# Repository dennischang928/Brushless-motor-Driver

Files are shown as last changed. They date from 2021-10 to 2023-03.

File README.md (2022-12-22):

# BLDC Driver

## Electronics

- MCU
  - STM32F103C8T6 (Blue pill)
    - Serial PIN
      - RX PA3 
      - TX PA2
- Mosfet
  - IRLR7843 (CMOSE)
- Mosfet Driver
  - DRV8303
    - PIN
      -  INHA PA8
      -  INLA PB6
      -  SO1 **PA1**
         
      -  INHB PA9
      -  INLB PB7
      -  SO2 **PA0**
         
      -  INHC PA10
      -  INLC PB8
         
      -  LED PC13
      -  EN_GATE PB12
      -  nFAULT PB13
      -  nOCTW PB14
      -  DC_CAL PB4
      -  SPI
         -  SPI1_NSS_PIN PA4
         -  SDO / MISO PA6
         -  We SDI / MOSI PA7
         -  SCLK PA5

- Encoder
  - AS5047P
    - PIN
      - A PA11
      - B PA12
      - Index PA15

**For Resistors and Ceramic Capacitors, use 0603 package.**

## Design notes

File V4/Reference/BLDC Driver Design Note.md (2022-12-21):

# BLDC Driver Design

## Rgate (Driving Current)

- The resistance of Rgate need to be optimized

  - Rgate is effecting the Rise time and Fall time of the driver output
  - 
  - 

  - If "tRiseFall" is too small, IDrive increased, which would lead to "**Inductive Spiking and Coupling From Switching on MOSFET**"

  - Our goal is to control IDrive at minimum, while tRiseFall is reasonable. 

- Steps:

  - Both the gate resistor and the Smart Gate Drive technology adjust the gate sink and source current

  - Choose a gate resistor that is equal to the reactance of the source inductance for critically damped

    performance and choose a gate resistor that is up to twice the reactance of the source inductance for underdamped performance as described in the *External Gate Resistor Design Guide for Gate Drivers* tech note

  - Alternatively, the resistors can also be chosen by using general calculations, observing the VGS waveform, and adjusting the value higher or lower for slower or faster slew rates, respectively

  - The Smart Gate Drive source or sink current can be calculated for a given FET, as described in Section 3.1.3

  - The process for choosing the gate resistor or IDRIVE is iterative and experimental

  - If the source and sink current can be controlled within the device, for example, Smart Gate Drive, it is still a

    good practice to add a 0-Ω resistor in series with the gate of the FET and replace with a non-zero resistor if further adjustment is required

## Buck Capacitor

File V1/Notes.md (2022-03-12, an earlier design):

# BLDC Driver

## Electronics

- MCU
  - STM32F103C8T6 (Blue pill)

- Mosfet
  - IRLR7843 (CMOSE)
- Mosfet Driver
  - DRV8305
    - PIN
      -  INHA PA8
      -  SO1 PB1
      -  INHB PA10
      -  SO2 PB0
      -  INHC PB7
      -  SO3 PA3
      -  LED PC13
      -  EN_GATE PB12
      -  nFAULT PB13
      -  nOCTW PB14
      -  DC_CAL PB4
      -  SPI
         -  SPI1_NSS_PIN PA4
         -  SDO / MISO PA6
         -  We SDI / MOSI PA7
         -  SCLK PA5

**For Resistors and Capacitors, use 0603 size.**

**Use T-stop Layer for non-綠油層**

## Programming

- MCU

  - Can Bus
    - Library
      [eXoCAN](https://github.com/exothink/eXoCAN)
      - 
- SPI Test
  Senduing write command: 0001011111110111
  Second try: 0 0010 11111110011
  ---------^^-Write Command-^^--------
  Sending read command: 1001000000000000
  Second try: 0
  ---------^^-Read Command-^^--------zZ

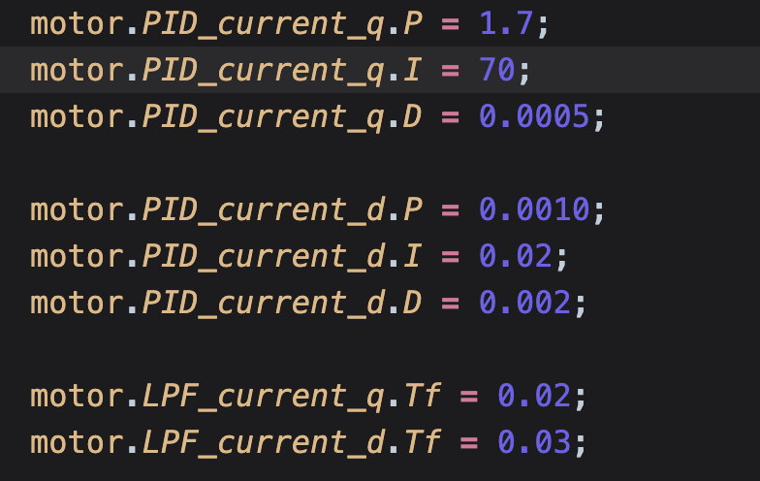
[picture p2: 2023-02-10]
V4/Programming/Sensored-FOC/CurrentSensored-Torque-Control/Screen Shot 2023-02-10 at 20.58.59.png

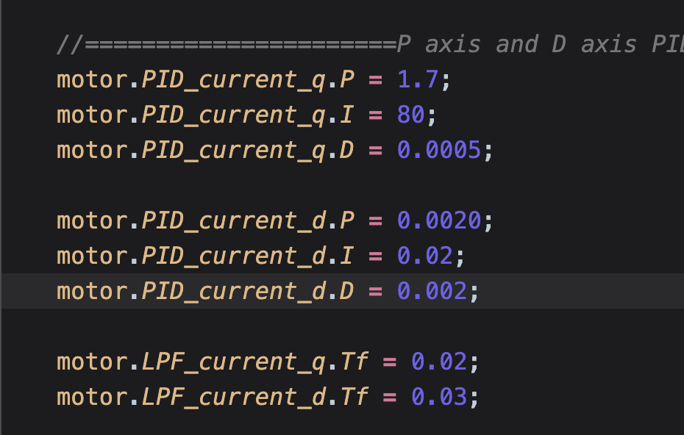
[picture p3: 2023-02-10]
V4/Programming/Sensored-FOC/CurrentSensored-Torque-Control/Screen Shot 2023-02-10 at 20.54.59.png

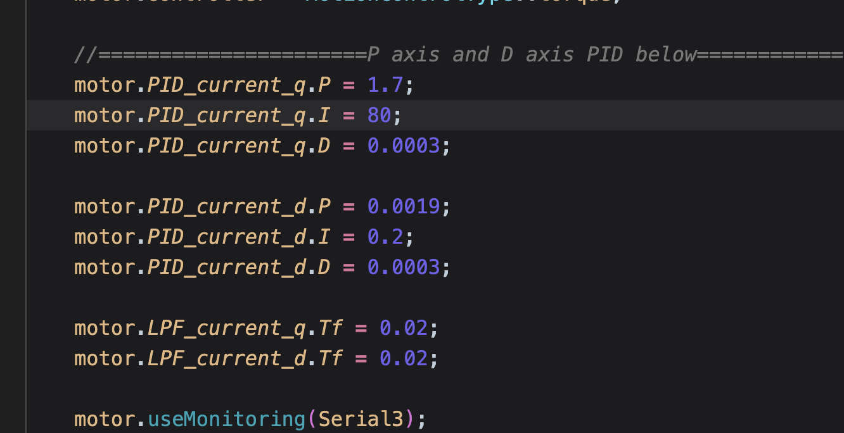
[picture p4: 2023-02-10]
V4/Programming/Sensored-FOC/CurrentSensored-Torque-Control/Screen Shot 2023-02-10 at 20.49.42.png

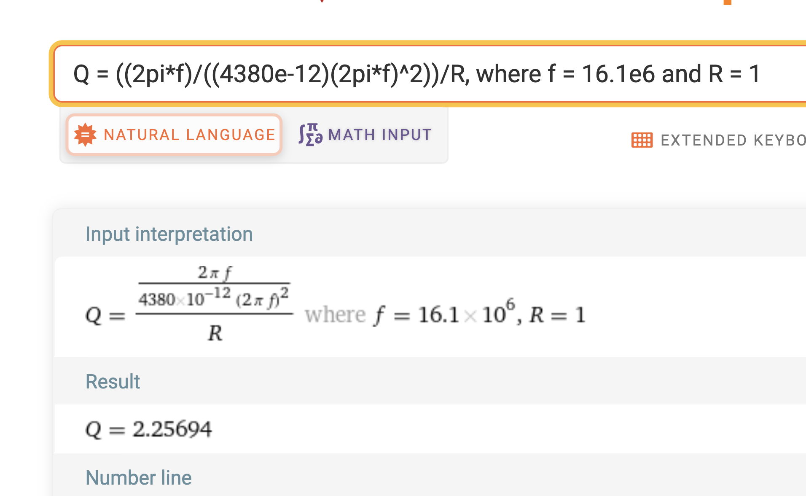
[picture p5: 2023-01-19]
V4/Reference/Screen Shot 2023-01-06 at 18.46.12.png

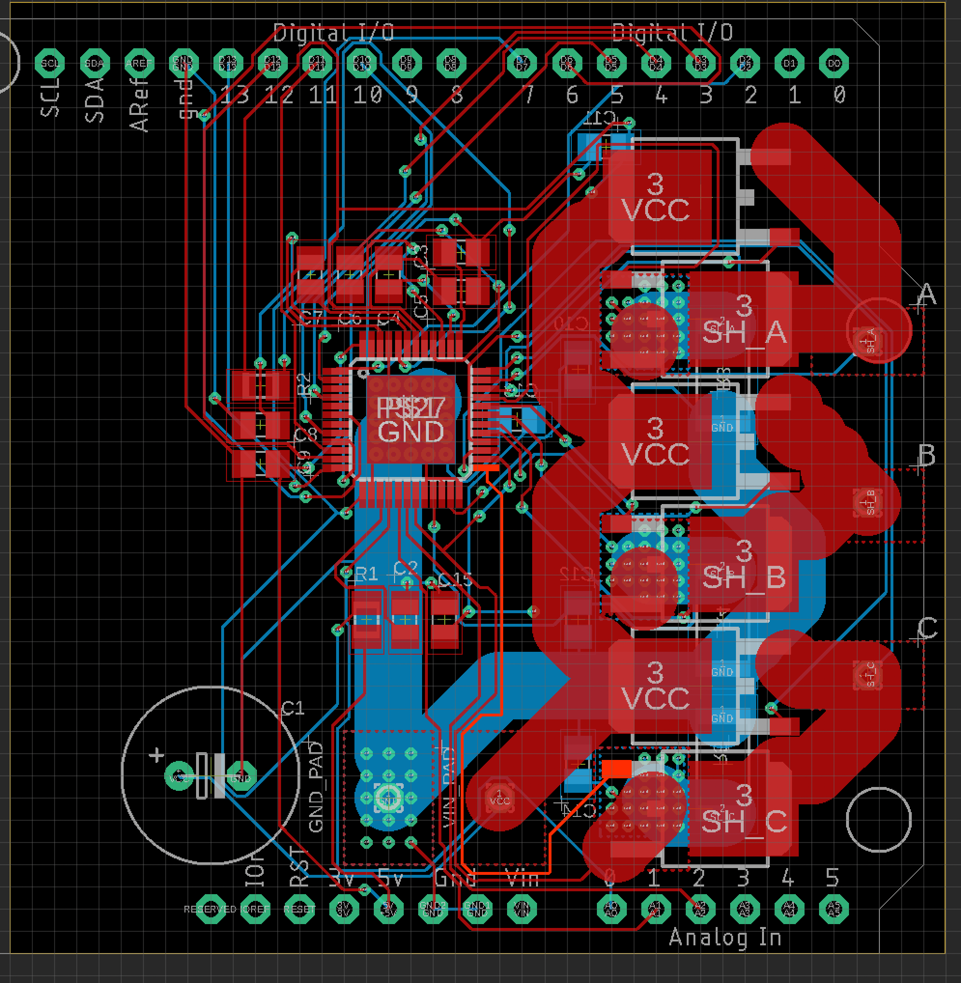
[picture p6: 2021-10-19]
Reference/BRD.png

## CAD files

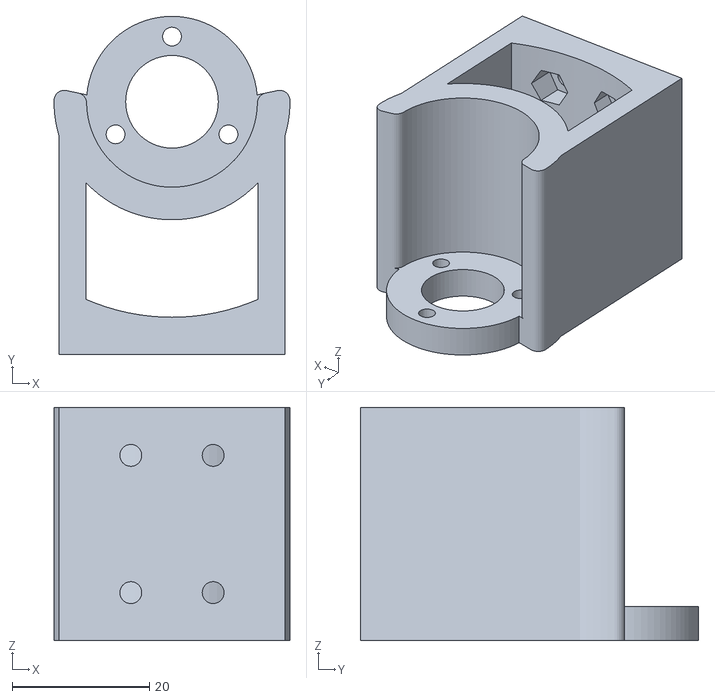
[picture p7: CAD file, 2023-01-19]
V4/CAD/Motor Holder/Body2.stl
34.4 x 49.3 x 34.0

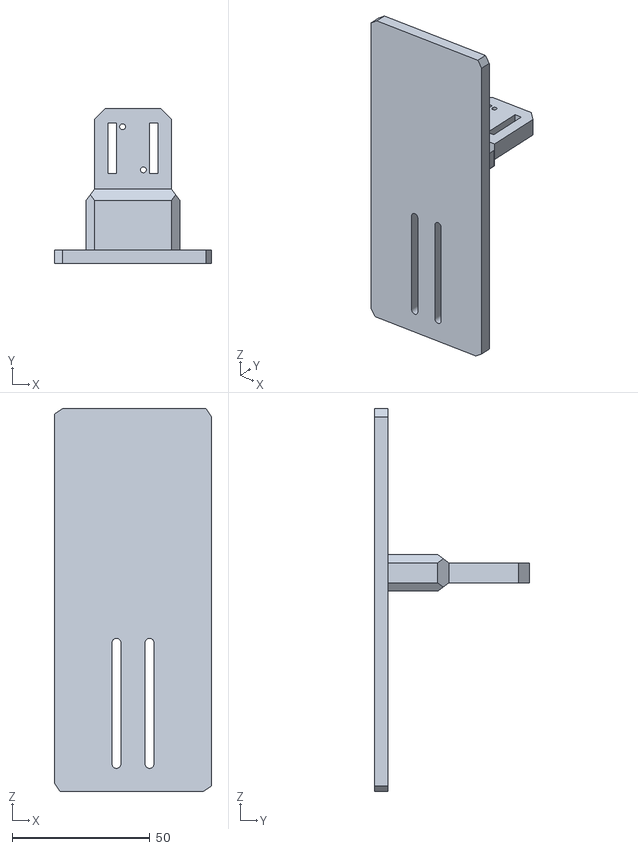
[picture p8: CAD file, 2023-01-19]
V4/CAD/Motor Holder/Body1.stl
57.0 x 56.4 x 139.0

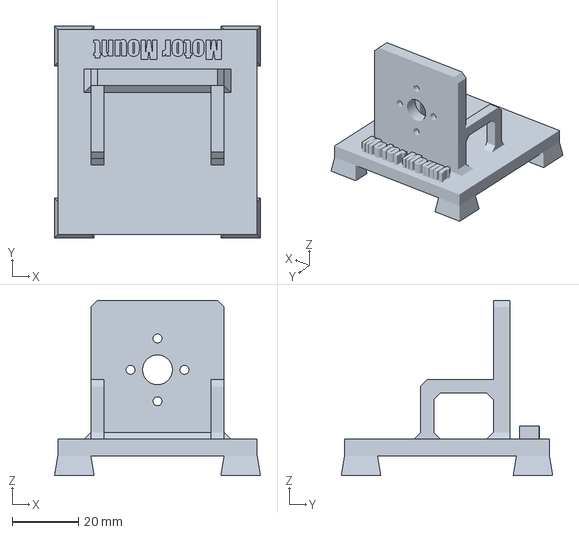
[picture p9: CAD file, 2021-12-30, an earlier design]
V1/Programming/Motor-Mount.3mf
62.3 x 64.0 x 53.0 mm

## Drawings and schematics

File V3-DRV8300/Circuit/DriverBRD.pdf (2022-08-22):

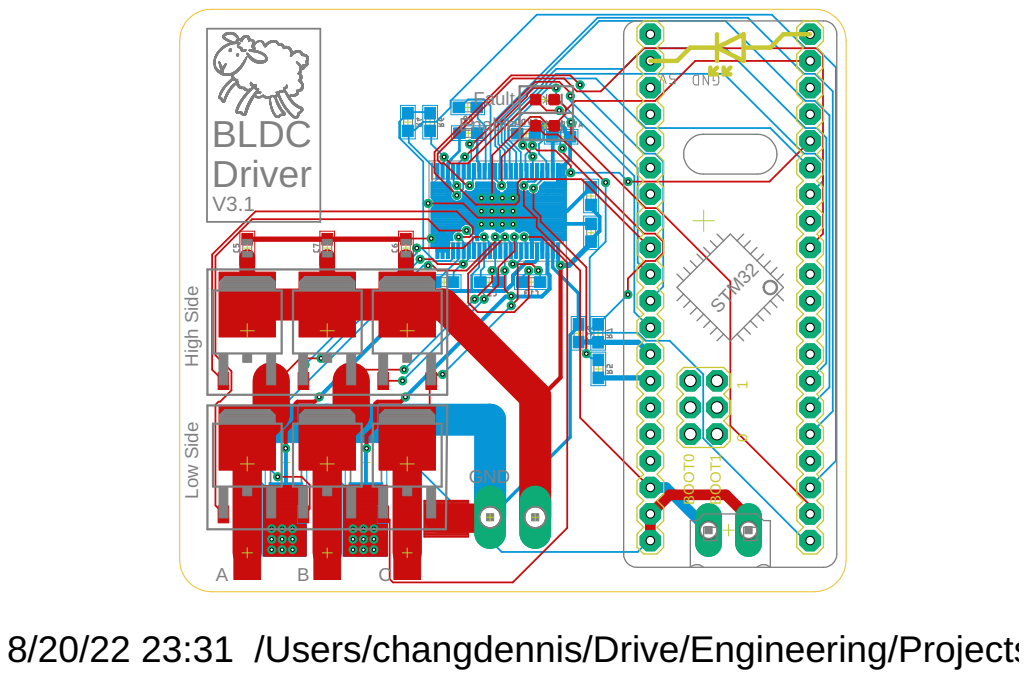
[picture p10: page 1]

High Side Low Side BLDC
Driver V3.1

8/20/22 23:31 /Users/changdennis/Drive/Engineering/Projects/Brushless Motor Driver/V3-DRV8300/Circuit/Driver.brd

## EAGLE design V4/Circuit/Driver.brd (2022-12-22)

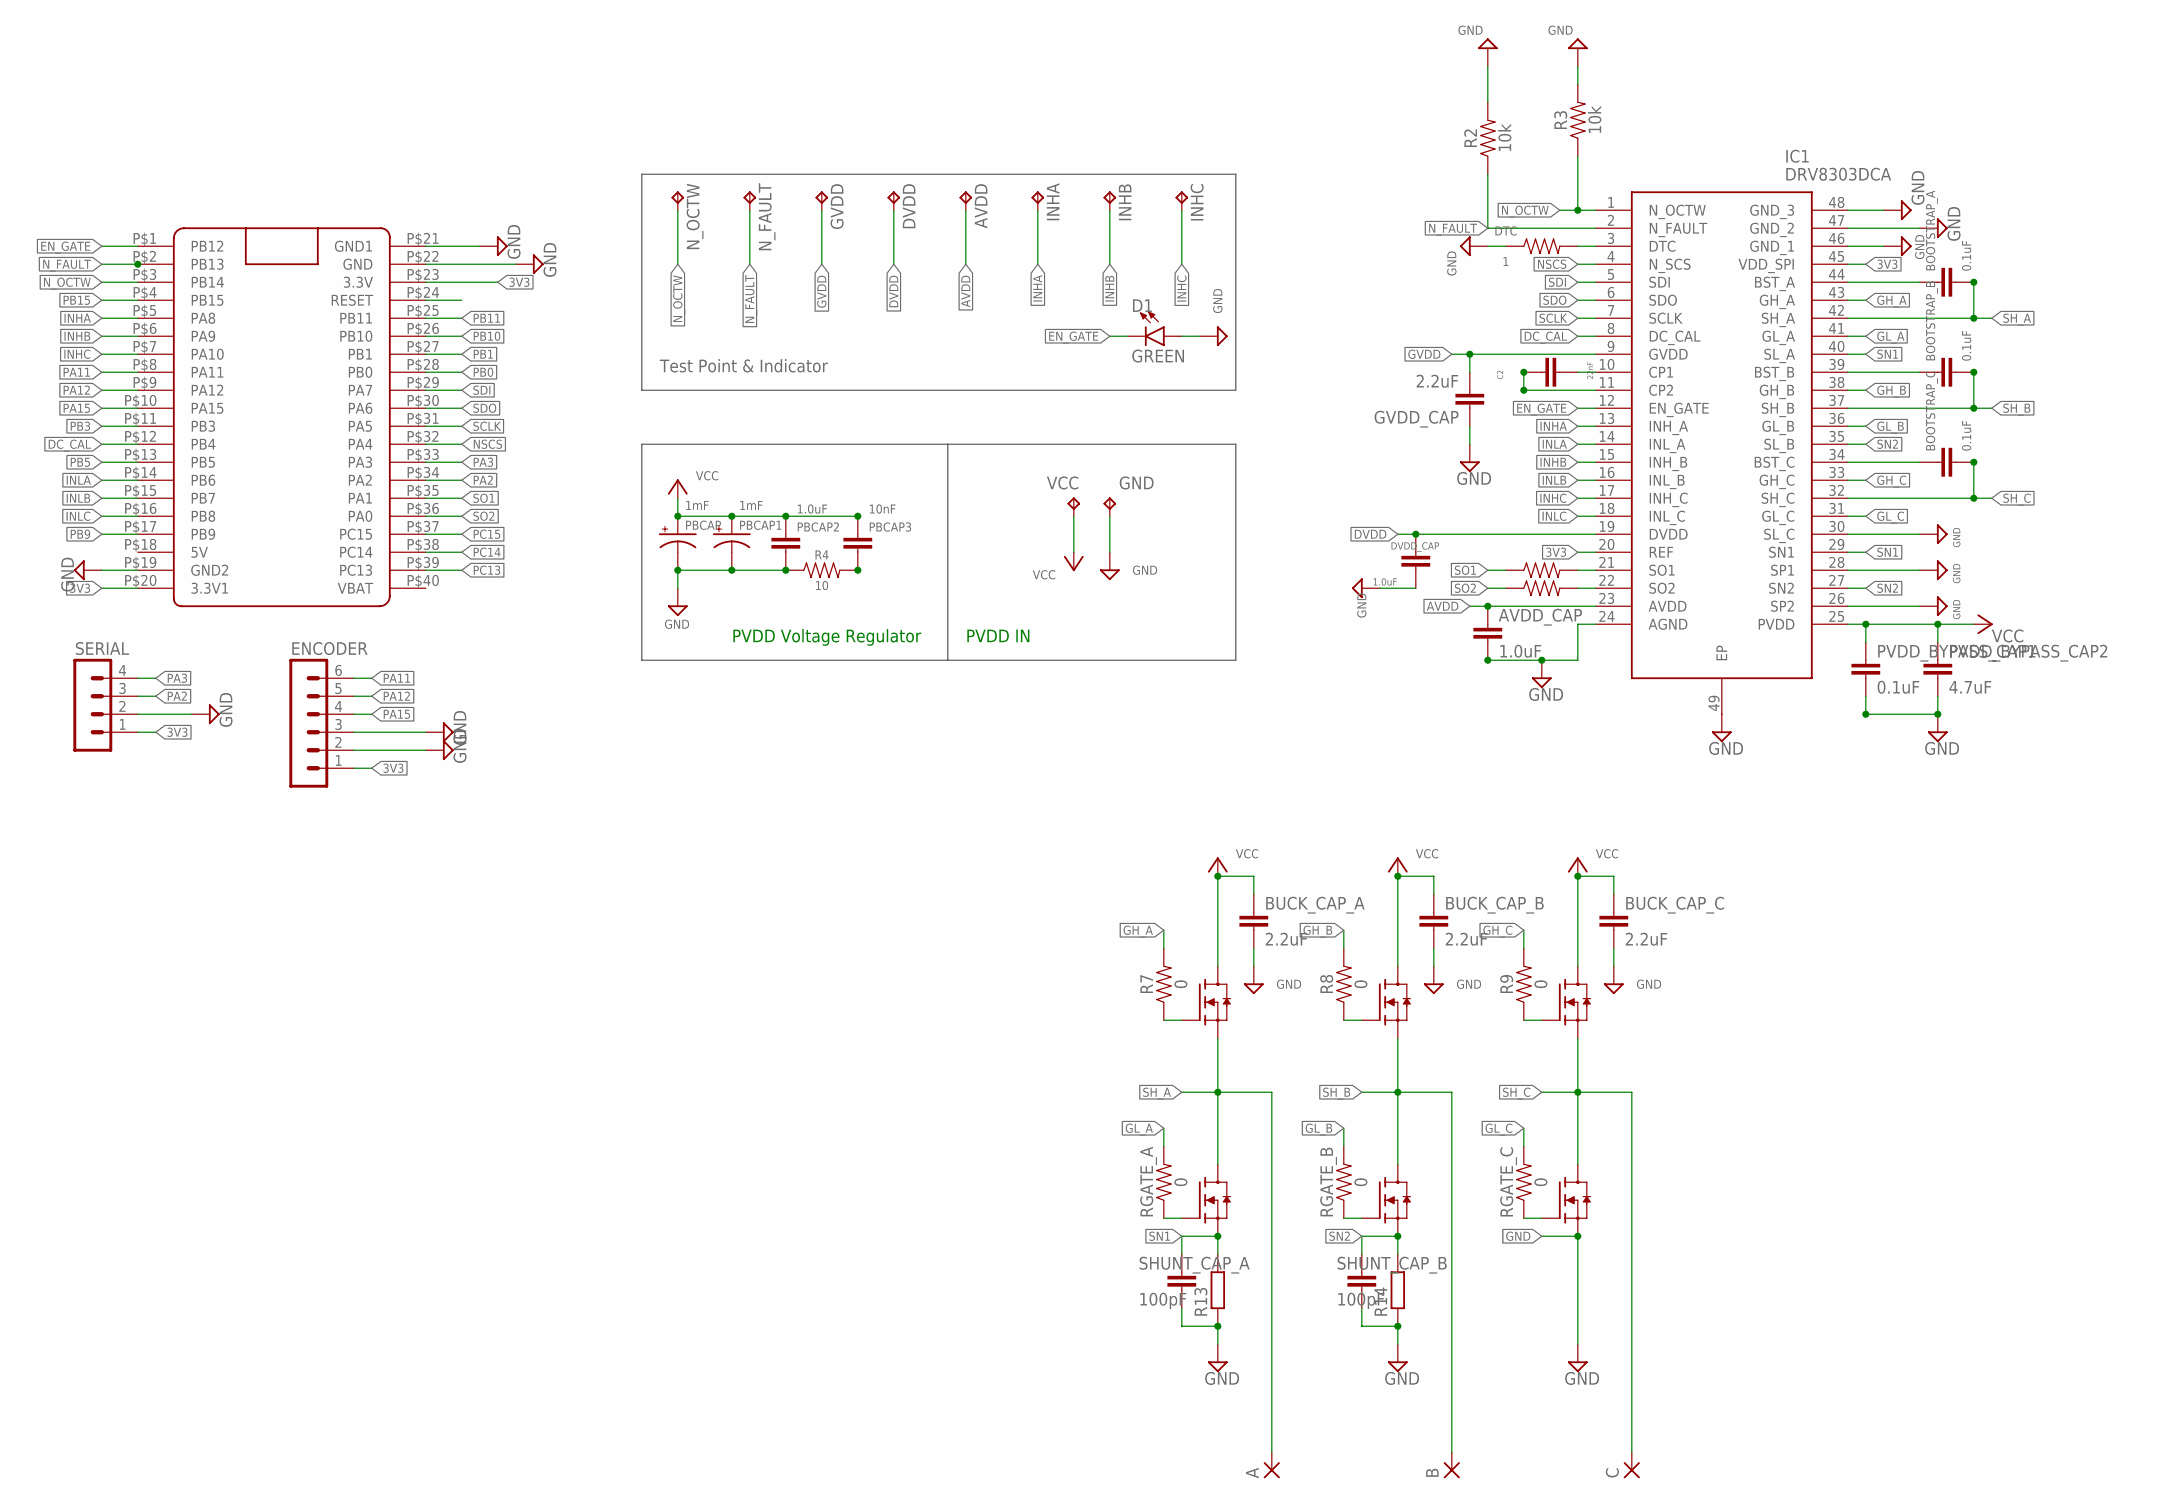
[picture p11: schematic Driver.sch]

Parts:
A: SMD5; SMD2,54-5,08
AVDD: TPTP16R; TP16R
AVDD_CAP: 1.0uF; 0603
B: SMD5; SMD2,54-5,08
BOOTSTRAP_A: 0.1uF; 0603
BOOTSTRAP_B: 0.1uF; 0603
BOOTSTRAP_C: 0.1uF; 0603
BUCK_CAP_A: 2.2uF; 0603
BUCK_CAP_B: 2.2uF; 0603
BUCK_CAP_C: 2.2uF; 0603
C: SMD5; SMD2,54-5,08
C2: 22nF; 0603
D1: GREEN; LED-0603
DTC: 1; 0603
DVDD: TPTP16R; TP16R
DVDD_CAP: 1.0uF; 0603
ENCODER: MA06-1
GND: TPPAD1-20Y; P1-20Y
GVDD: TPTP16R; TP16R
GVDD_CAP: 2.2uF; 0603
HA: IRLR7843; TO252
HB: IRLR7843; TO252
HC: IRLR7843; TO252
IC1: DRV8303DCA; SOP50P810X120-49N
INHA: TPTP16R; TP16R
INHB: TPTP16R; TP16R
INHC: TPTP16R; TP16R
LA: IRLR7843; TO252
LB: IRLR7843; TO252
LC: IRLR7843; TO252
N_FAULT: TPTP16R; TP16R
N_OCTW: TPTP16R; TP16R
PBCAP, PBCAP1: 1mF; CPOL-RADIAL-5MM-10MM
PBCAP2: 1.0uF; 0603
PBCAP3: 10nF; 0603
PVDD_BYPASS_CAP1: 0.1uF; 0603
PVDD_BYPASS_CAP2: 4.7uF; 0603
R2, R3: 10k; 0603
R4: 10; 0603
R5, R6: 47; 0603
R7, R8, R9: 0; 0603
R13, R14: R-EU_R2512; R2512
RGATE_A: 0; 0603
RGATE_B: 0; 0603
RGATE_C: 0; 0603
SERIAL: MA04-1
SHUNT_CAP_A: 100pF; 0603
SHUNT_CAP_B: 100pF; 0603
U$1: BLUE_PILLADVANCED; BLUE_PILL_ADV
VCC: TPPAD1-20Y; P1-20Y

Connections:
3V3: ENCODER.1, IC1.20 (REF), IC1.45 (VDD_SPI), SERIAL.1, U$1.P$20 (3.3V1), U$1.P$23 (3.3V)
AVDD: AVDD.TP, AVDD_CAP.1, IC1.23 (AVDD)
DC_CAL: IC1.8 (DC_CAL), U$1.P$12 (PB4)
DVDD: DVDD.TP, DVDD_CAP.1, IC1.19 (DVDD)
EN_GATE: D1.C, IC1.12 (EN_GATE), U$1.P$1 (PB12)
GH_A: IC1.43 (GH_A), R7.2
GH_B: IC1.38 (GH_B), R8.2
GH_C: IC1.33 (GH_C), R9.2
GL_A: IC1.41 (GL_A), RGATE_A.2
GL_B: IC1.36 (GL_B), RGATE_B.2
GL_C: IC1.31 (GL_C), RGATE_C.2
GND: AVDD_CAP.2, BUCK_CAP_A.2, BUCK_CAP_B.2, BUCK_CAP_C.2, D1.A, DTC.1, DVDD_CAP.2, ENCODER.2, ENCODER.3, GND.TP, GVDD_CAP.1, IC1.24 (AGND), IC1.26 (SP2), IC1.28 (SP1), IC1.30 (SL_C), IC1.46 (GND_1), IC1.47 (GND_2), IC1.48 (GND_3), IC1.49 (EP), LC.2 (S), PBCAP.-, PBCAP1.-, PBCAP2.2, PVDD_BYPASS_CAP1.2, PVDD_BYPASS_CAP2.2, R2.2, R3.2, R4.1, R13.1, R14.1, SERIAL.2, SHUNT_CAP_A.2, SHUNT_CAP_B.2, U$1.P$19 (GND2), U$1.P$21 (GND1), U$1.P$22 (GND)
GVDD: GVDD.TP, GVDD_CAP.2, IC1.9 (GVDD)
INHA: IC1.13 (INH_A), INHA.TP, U$1.P$5 (PA8)
INHB: IC1.15 (INH_B), INHB.TP, U$1.P$6 (PA9)
INHC: IC1.17 (INH_C), INHC.TP, U$1.P$7 (PA10)
INLA: IC1.14 (INL_A), U$1.P$14 (PB6)
INLB: IC1.16 (INL_B), U$1.P$15 (PB7)
INLC: IC1.18 (INL_C), U$1.P$16 (PB8)
unnamed: DTC.2, IC1.3 (DTC)
unnamed: PBCAP3.2, R4.2
unnamed: BOOTSTRAP_A.1, IC1.44 (BST_A)
unnamed: HA.1 (G), R7.1
unnamed: HB.1 (G), R8.1
unnamed: HC.1 (G), R9.1
unnamed: BOOTSTRAP_B.1, IC1.39 (BST_B)
unnamed: LC.1 (G), RGATE_C.1
unnamed: BOOTSTRAP_C.1, IC1.34 (BST_C)
unnamed: LB.1 (G), RGATE_B.1
unnamed: LA.1 (G), RGATE_A.1
unnamed: C2.2, IC1.10 (CP1)
unnamed: C2.1, IC1.11 (CP2)
NSCS: IC1.4 (N_SCS), U$1.P$32 (PA4)
N_FAULT: IC1.2 (N_FAULT), N_FAULT.TP, R2.1, U$1.P$2 (PB13)
N_OCTW: IC1.1 (N_OCTW), N_OCTW.TP, R3.1, U$1.P$3 (PB14)
PA2: SERIAL.3, U$1.P$34 (PA2)
PA3: SERIAL.4, U$1.P$33 (PA3)
PA11: ENCODER.6, U$1.P$8 (PA11)
PA12: ENCODER.5, U$1.P$9 (PA12)
PA15: ENCODER.4, U$1.P$10 (PA15)
PB0: U$1.P$28 (PB0)
PB1: U$1.P$27 (PB1)
PB3: U$1.P$11 (PB3)
PB5: U$1.P$13 (PB5)
PB9: U$1.P$17 (PB9)
PB10: U$1.P$26 (PB10)
PB11: U$1.P$25 (PB11)
PB15: U$1.P$4 (PB15)
PC13: U$1.P$39 (PC13)
PC14: U$1.P$38 (PC14)
PC15: U$1.P$37 (PC15)
SCLK: IC1.7 (SCLK), U$1.P$31 (PA5)
SDI: IC1.5 (SDI), U$1.P$29 (PA7)
SDO: IC1.6 (SDO), U$1.P$30 (PA6)
SH_A: A.1, BOOTSTRAP_A.2, HA.2 (S), IC1.42 (SH_A), LA.3 (D)
SH_B: B.1, BOOTSTRAP_B.2, HB.2 (S), IC1.37 (SH_B), LB.3 (D)
SH_C: BOOTSTRAP_C.2, C.1, HC.2 (S), IC1.32 (SH_C), LC.3 (D)
SN1: IC1.29 (SN1), IC1.40 (SL_A), LA.2 (S), R13.2, SHUNT_CAP_A.1
SN2: IC1.27 (SN2), IC1.35 (SL_B), LB.2 (S), R14.2, SHUNT_CAP_B.1
SO1: R5.1, U$1.P$35 (PA1)
SO1B: IC1.21 (SO1), R5.2
SO2: R6.1, U$1.P$36 (PA0)
SO2B: IC1.22 (SO2), R6.2
VCC: BUCK_CAP_A.1, BUCK_CAP_B.1, BUCK_CAP_C.1, HA.3 (D), HB.3 (D), HC.3 (D), IC1.25 (PVDD), PBCAP.+, PBCAP1.+, PBCAP2.1, PBCAP3.1, PVDD_BYPASS_CAP1.1, PVDD_BYPASS_CAP2.1, VCC.TP

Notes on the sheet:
Test Point & Indicator
PVDD Voltage Regulator
PVDD IN

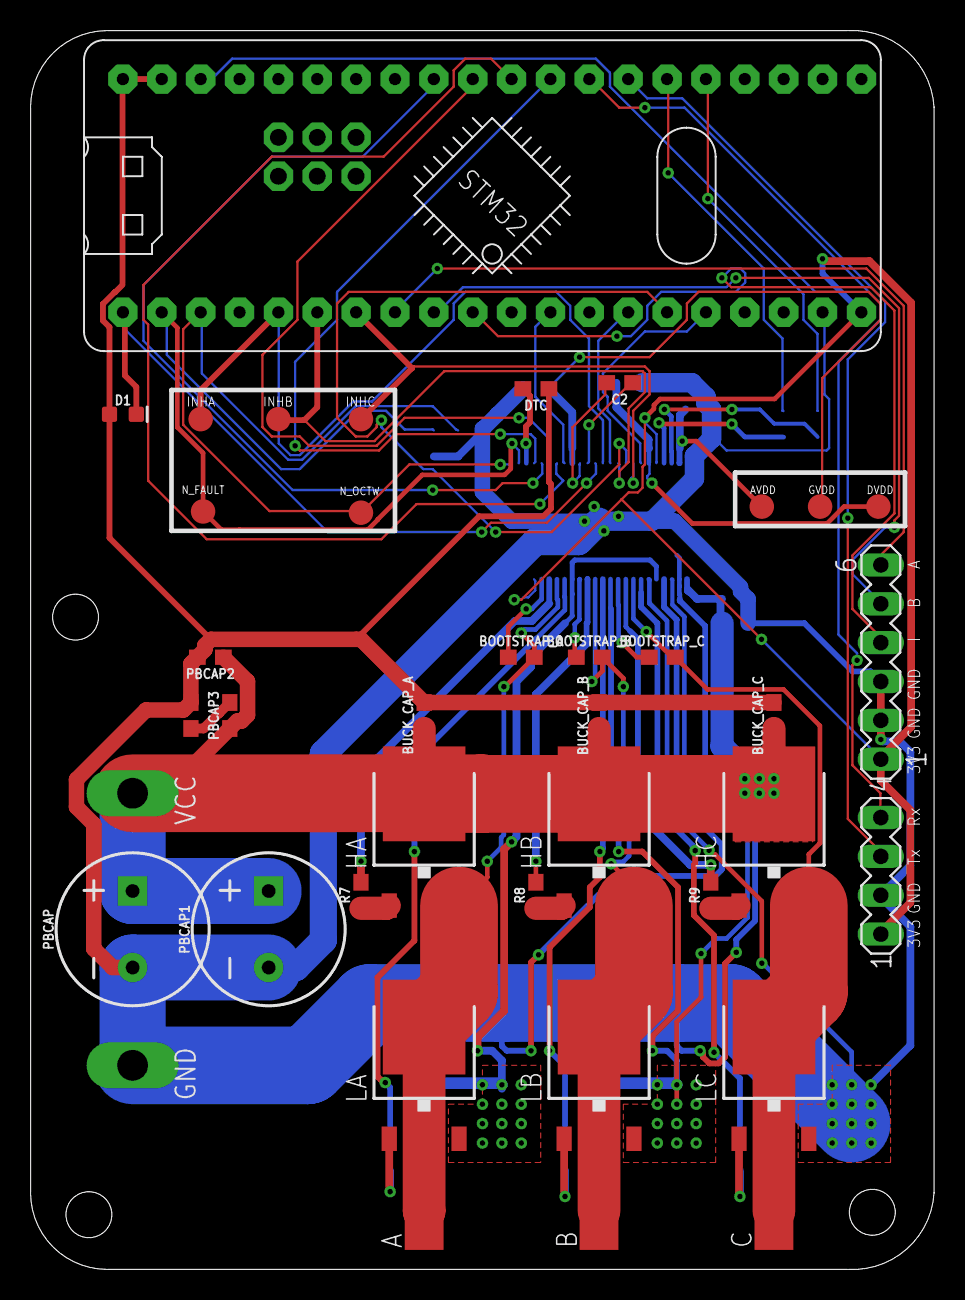
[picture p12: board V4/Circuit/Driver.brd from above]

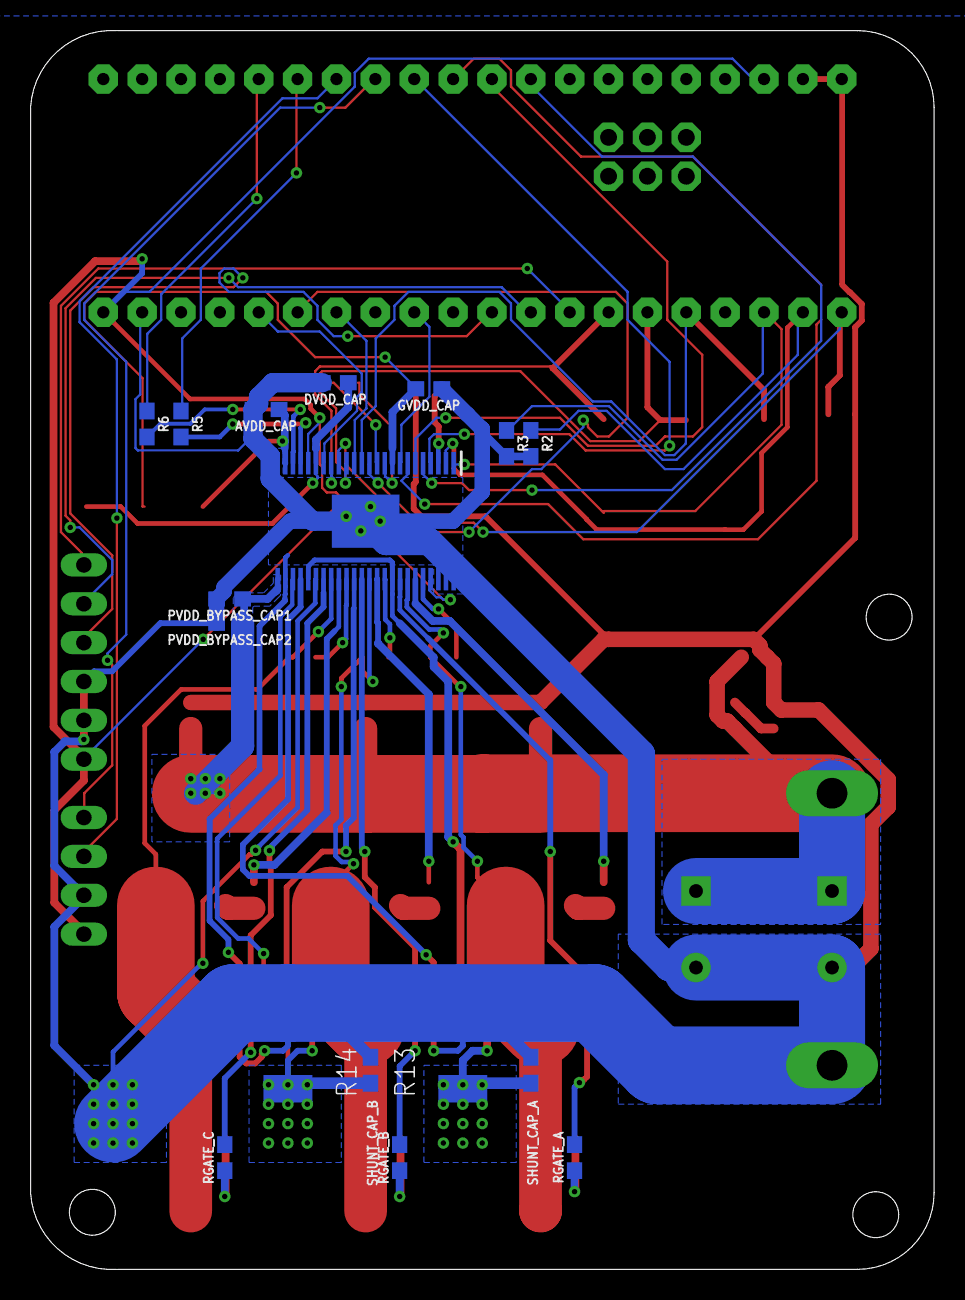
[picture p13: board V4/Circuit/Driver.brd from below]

Board: 2 copper layers, 59.0 x 81.0 mm, 56 parts (17 on the bottom side), 53 nets.

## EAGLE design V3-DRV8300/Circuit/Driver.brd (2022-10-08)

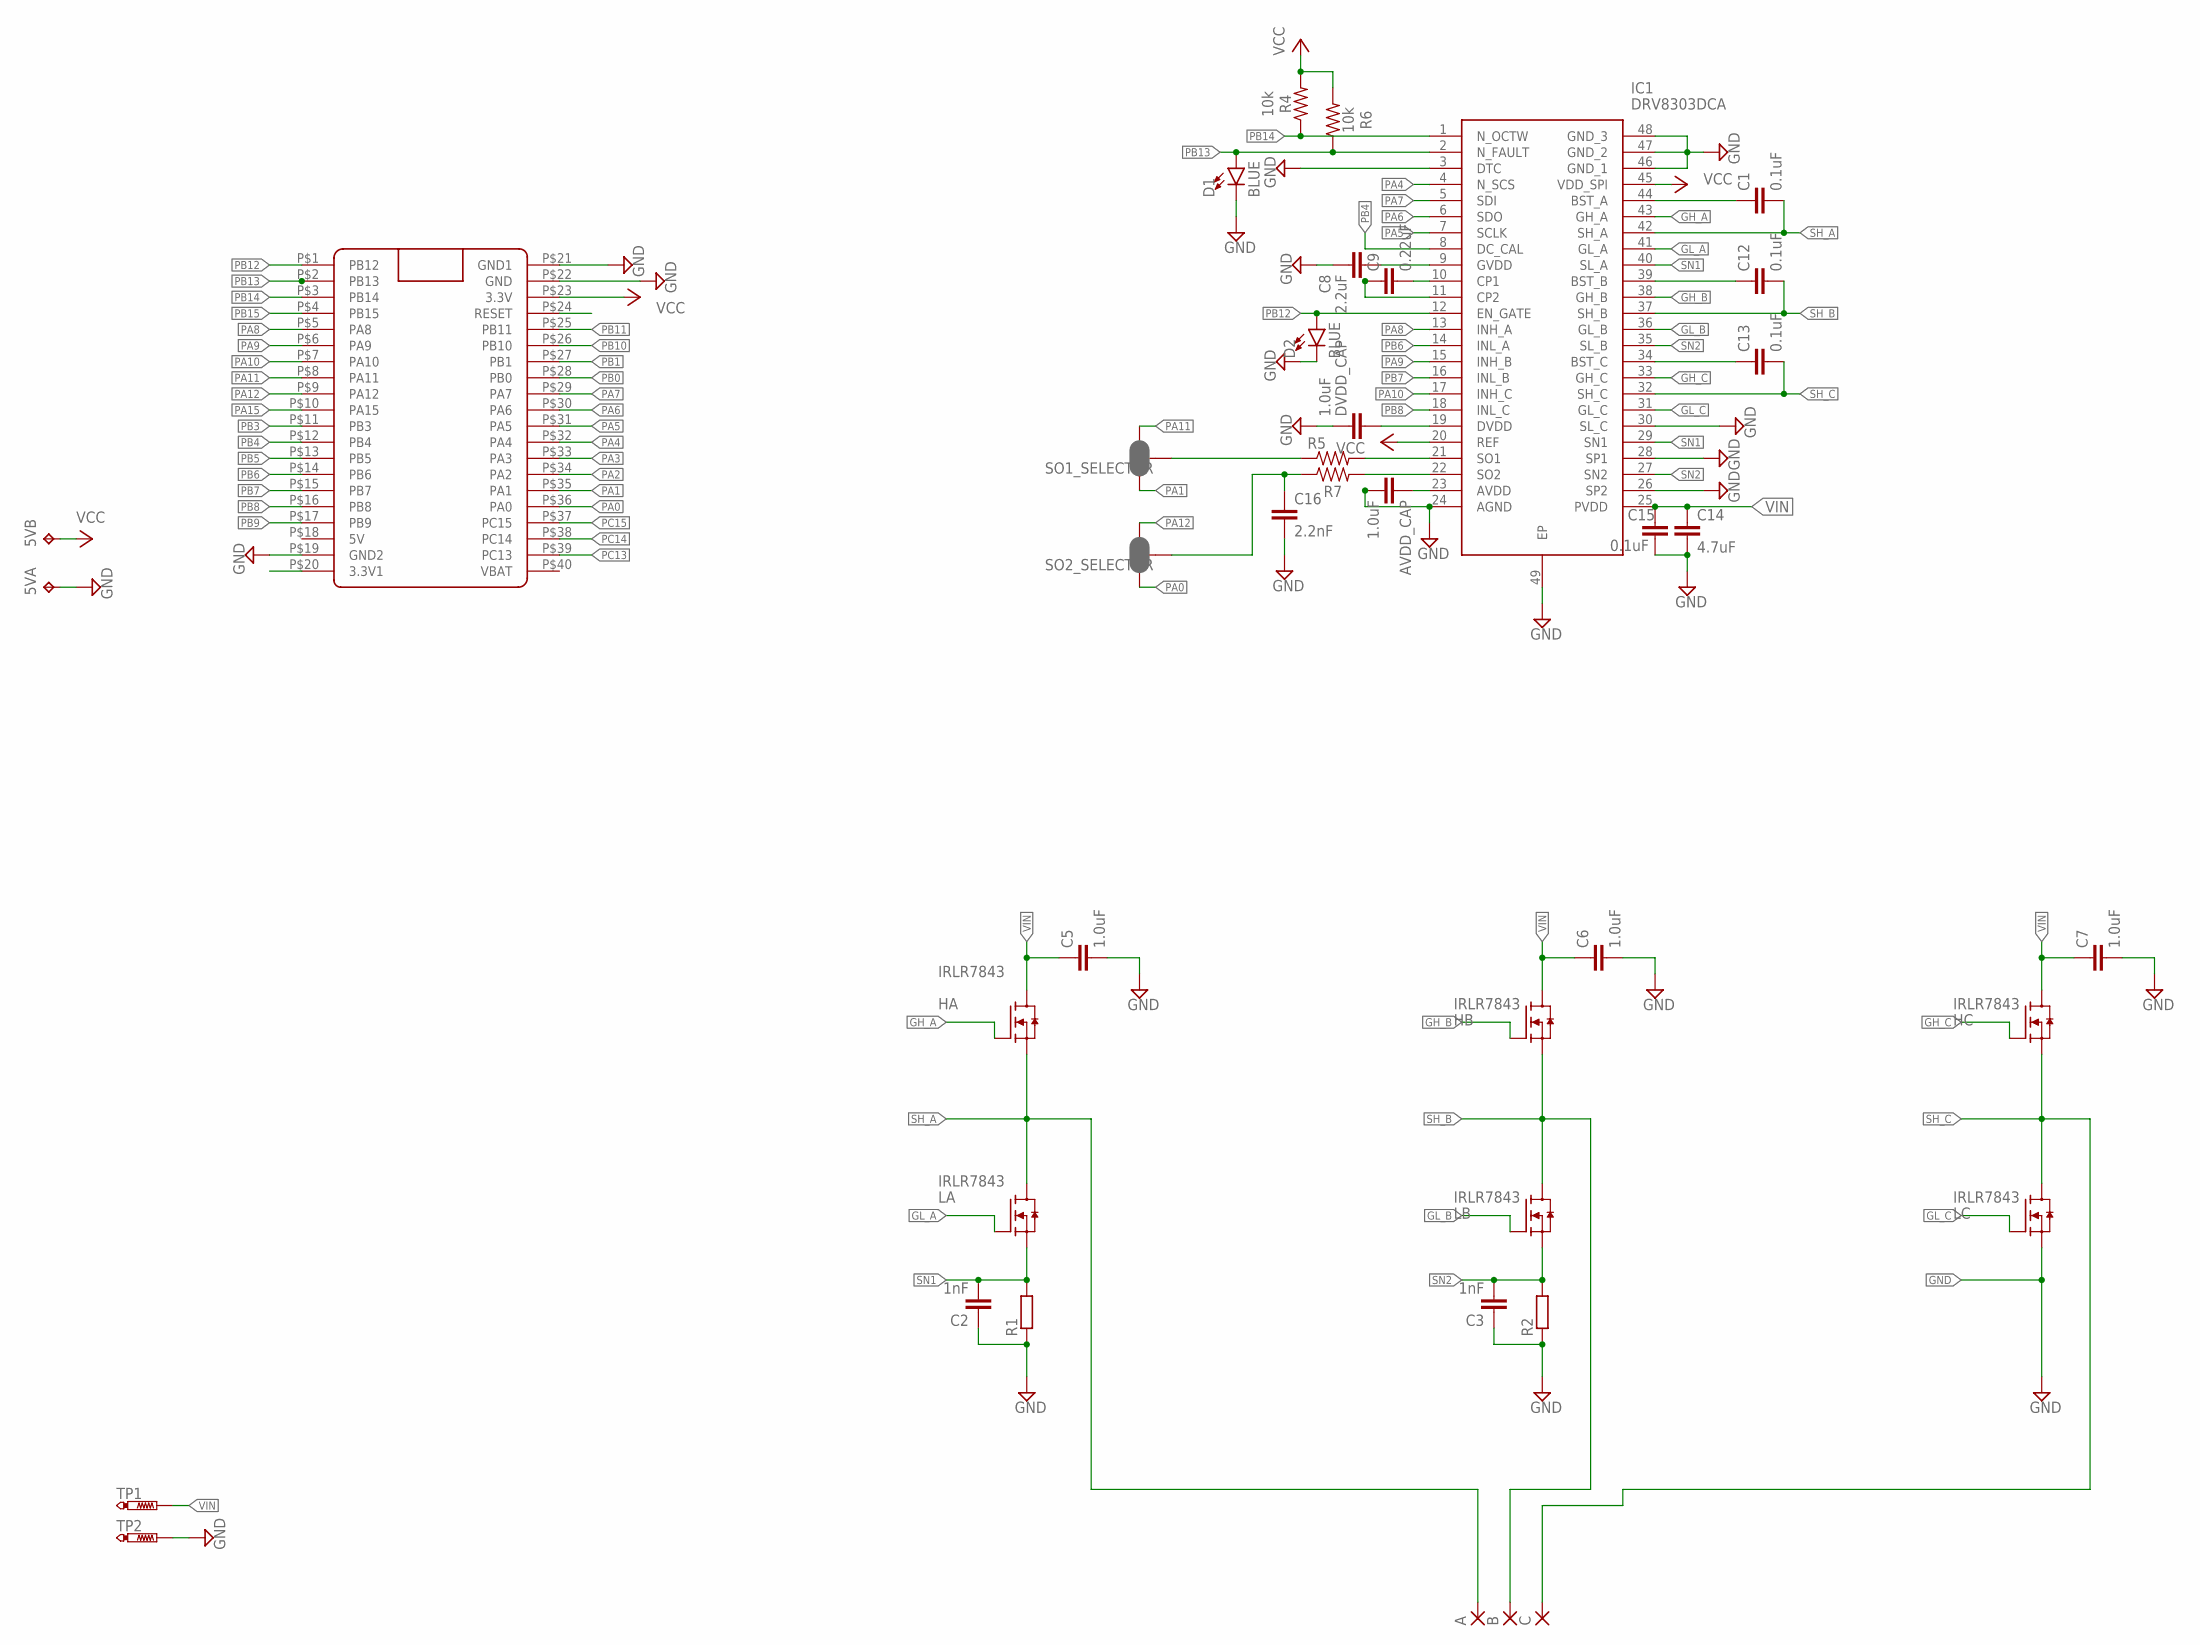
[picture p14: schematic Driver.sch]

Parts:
5V: TP2P2-38-17; P2-38-17
A: SMD5; SMD2,54-5,08
AVDD_CAP: 1.0uF; 0603
B: SMD5; SMD2,54-5,08
C: SMD5; SMD2,54-5,08
C1, C12, C13, C15: 0.1uF; 0603
C2, C3: 1nF; 0603
C5, C6, C7: 1.0uF; 0603
C8: 2.2uF; 0603
C9: 0.22uF; 0603
C14: 4.7uF; 0603
C16: 2.2nF; 0603
D1, D2: BLUE; LED-0603
DVDD_CAP: 1.0uF; 0603
HA: IRLR7843; TO252
HB: IRLR7843; TO252
HC: IRLR7843; TO252
IC1: DRV8303DCA; SOP50P810X120-49N
LA: IRLR7843; TO252
LB: IRLR7843; TO252
LC: IRLR7843; TO252
R1, R2: R-EU_R2512; R2512
R4, R6: 10k; 0603
R5, R7: 0; 0603
SO1_SELECTOR, SO2_SELECTOR: JUMPER-SMT_3_2-NC_PASTE_SILK; SMT-JUMPER_3_2-NC_PASTE_SILK
TP1, TP2: PTR1PAD1-20Y; P1-20Y
U$1: BLUE_PILLADVANCED; BLUE_PILL_ADV

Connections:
GH_A: HA.1 (G), IC1.43 (GH_A)
GH_B: HB.1 (G), IC1.38 (GH_B)
GH_C: HC.1 (G), IC1.33 (GH_C)
GL_A: IC1.41 (GL_A), LA.1 (G)
GL_B: IC1.36 (GL_B), LB.1 (G)
GL_C: IC1.31 (GL_C), LC.1 (G)
GND: 5V.TP-1, AVDD_CAP.2, C2.1, C3.1, C5.2, C6.2, C7.2, C8.2, C14.2, C15.2, C16.2, D1.C, D2.C, DVDD_CAP.1, IC1.3 (DTC), IC1.24 (AGND), IC1.26 (SP2), IC1.28 (SP1), IC1.30 (SL_C), IC1.46 (GND_1), IC1.47 (GND_2), IC1.48 (GND_3), IC1.49 (EP), LC.2 (S), R1.1, R2.1, TP2.TP, U$1.P$19 (GND2), U$1.P$21 (GND1), U$1.P$22 (GND)
unnamed: IC1.21 (SO1), R5.2
unnamed: C1.1, IC1.44 (BST_A)
unnamed: IC1.22 (SO2), R7.2
unnamed: C12.1, IC1.39 (BST_B)
unnamed: C13.1, IC1.34 (BST_C)
unnamed: C8.1, IC1.9 (GVDD)
unnamed: C9.2, IC1.10 (CP1)
unnamed: C9.1, IC1.11 (CP2)
unnamed: DVDD_CAP.2, IC1.19 (DVDD)
unnamed: AVDD_CAP.1, IC1.23 (AVDD)
PA0: SO2_SELECTOR.1, U$1.P$36 (PA0)
PA1: SO1_SELECTOR.1, U$1.P$35 (PA1)
PA2: U$1.P$34 (PA2)
PA3: U$1.P$33 (PA3)
PA4: IC1.4 (N_SCS), U$1.P$32 (PA4)
PA5: IC1.7 (SCLK), U$1.P$31 (PA5)
PA6: IC1.6 (SDO), U$1.P$30 (PA6)
PA7: IC1.5 (SDI), U$1.P$29 (PA7)
PA8: IC1.13 (INH_A), U$1.P$5 (PA8)
PA9: IC1.15 (INH_B), U$1.P$6 (PA9)
PA10: IC1.17 (INH_C), U$1.P$7 (PA10)
PA11: SO1_SELECTOR.3, U$1.P$8 (PA11)
PA12: SO2_SELECTOR.3, U$1.P$9 (PA12)
PA15: U$1.P$10 (PA15)
PB0: U$1.P$28 (PB0)
PB1: U$1.P$27 (PB1)
PB3: U$1.P$11 (PB3)
PB4: IC1.8 (DC_CAL), U$1.P$12 (PB4)
PB5: U$1.P$13 (PB5)
PB6: IC1.14 (INL_A), U$1.P$14 (PB6)
PB7: IC1.16 (INL_B), U$1.P$15 (PB7)
PB8: IC1.18 (INL_C), U$1.P$16 (PB8)
PB9: U$1.P$17 (PB9)
PB10: U$1.P$26 (PB10)
PB11: U$1.P$25 (PB11)
PB12: D2.A, IC1.12 (EN_GATE), U$1.P$1 (PB12)
PB13: D1.A, IC1.2 (N_FAULT), R6.1, U$1.P$2 (PB13)
PB14: IC1.1 (N_OCTW), R4.1, U$1.P$3 (PB14)
PB15: U$1.P$4 (PB15)
PC13: U$1.P$39 (PC13)
PC14: U$1.P$38 (PC14)
PC15: U$1.P$37 (PC15)
SH_A: A.1, C1.2, HA.2 (S), IC1.42 (SH_A), LA.3 (D)
SH_B: B.1, C12.2, HB.2 (S), IC1.37 (SH_B), LB.3 (D)
SH_C: C.1, C13.2, HC.2 (S), IC1.32 (SH_C), LC.3 (D)
SN1: C2.2, IC1.29 (SN1), IC1.40 (SL_A), LA.2 (S), R1.2
SN2: C3.2, IC1.27 (SN2), IC1.35 (SL_B), LB.2 (S), R2.2
SO1: R5.1, SO1_SELECTOR.2
SO2: C16.1, R7.1, SO2_SELECTOR.2
VCC: 5V.TP-2, IC1.20 (REF), IC1.45 (VDD_SPI), R4.2, R6.2, U$1.P$23 (3.3V)
VIN: C5.1, C6.1, C7.1, C14.1, C15.1, HA.3 (D), HB.3 (D), HC.3 (D), IC1.25 (PVDD), TP1.TP

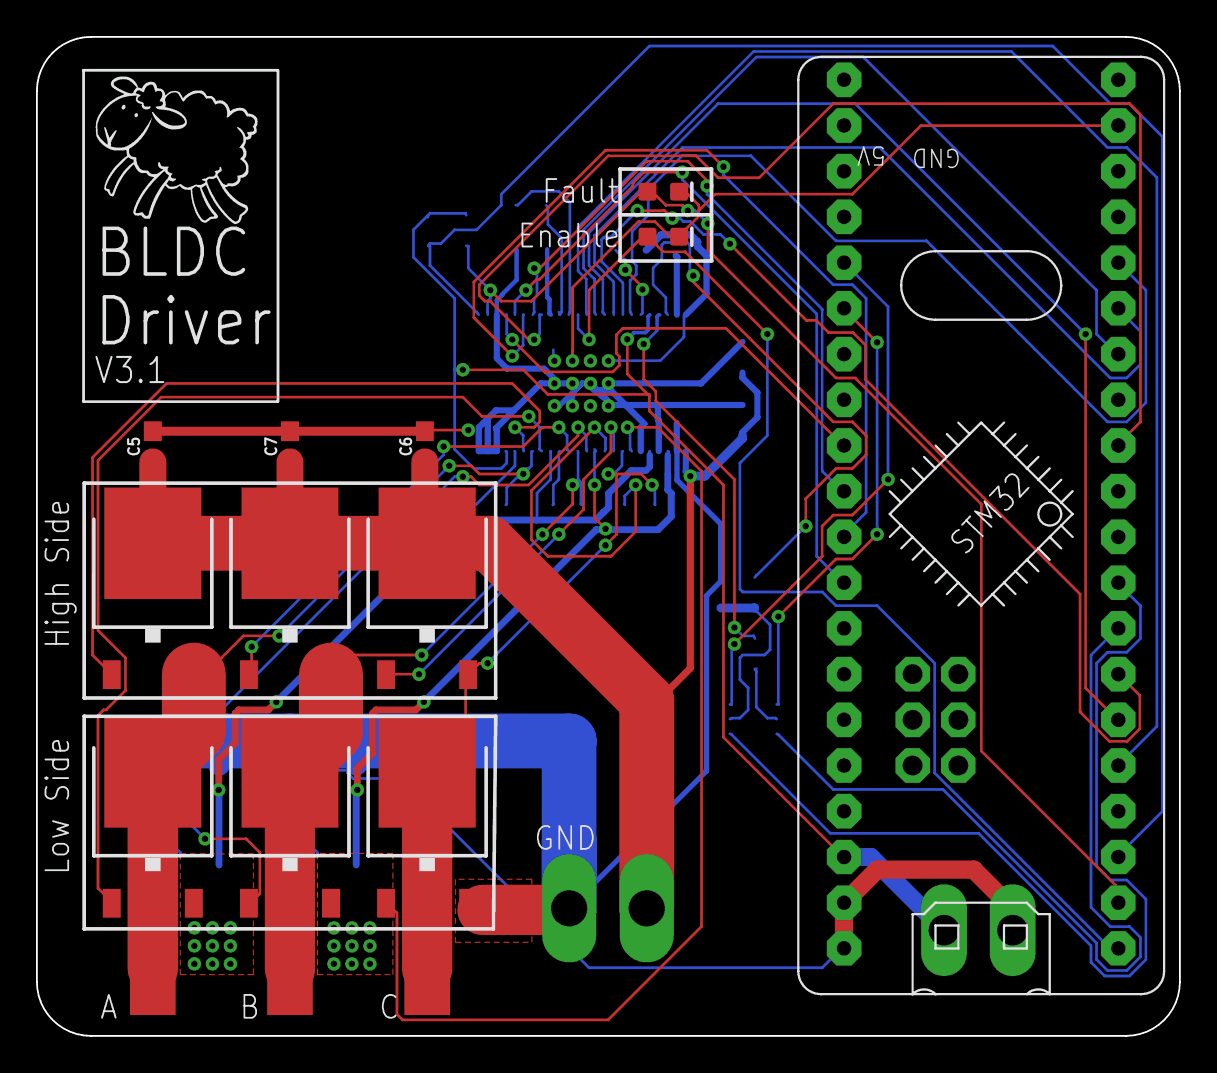
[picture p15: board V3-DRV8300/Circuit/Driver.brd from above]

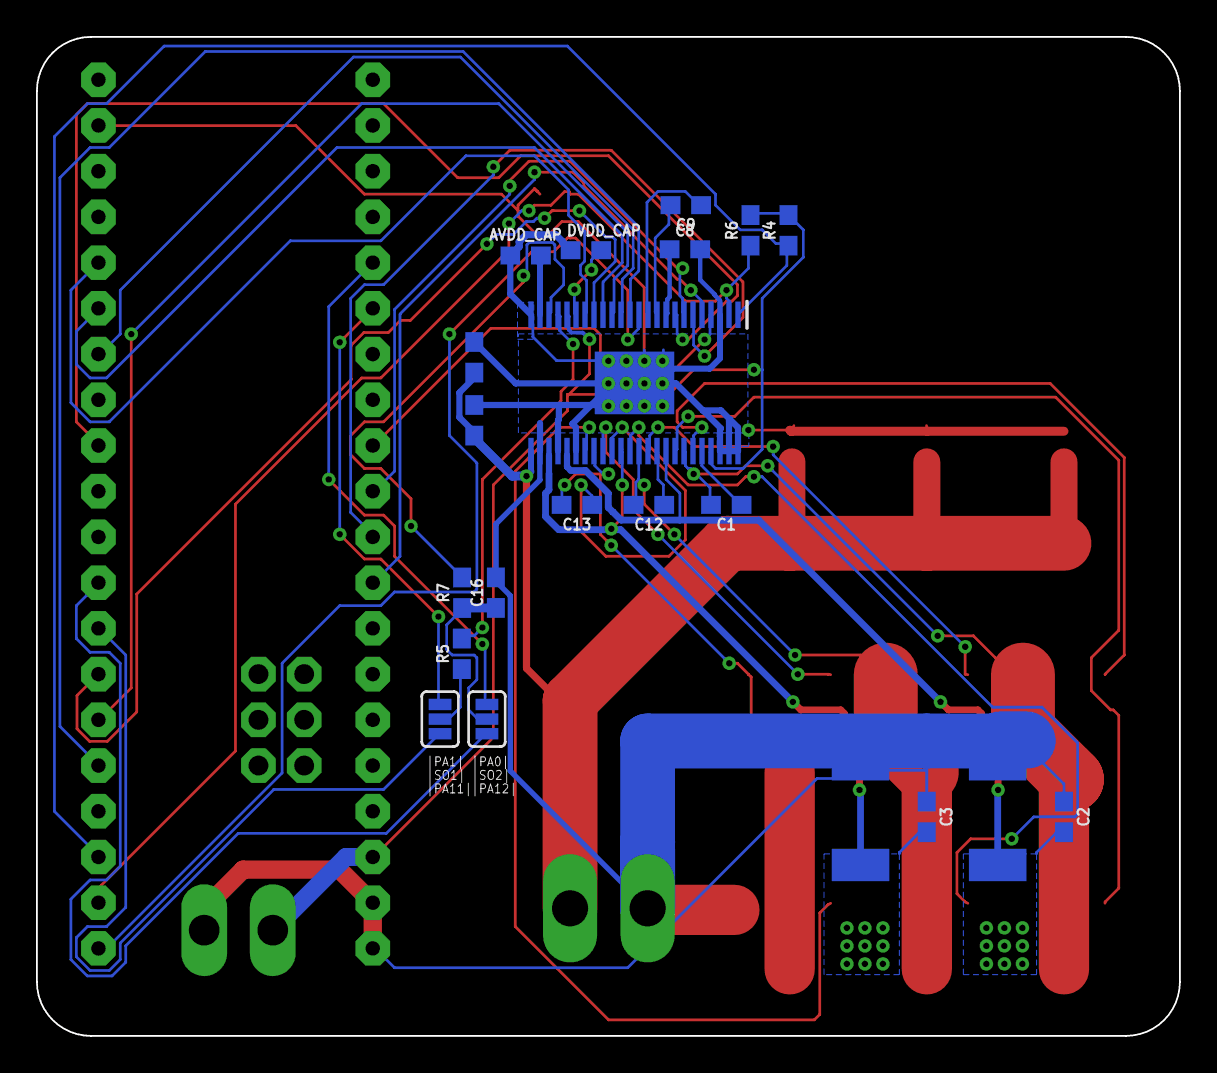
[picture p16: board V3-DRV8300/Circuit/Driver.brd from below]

Board: 2 copper layers, 63.5 x 55.5 mm, 39 parts (21 on the bottom side), 44 nets.

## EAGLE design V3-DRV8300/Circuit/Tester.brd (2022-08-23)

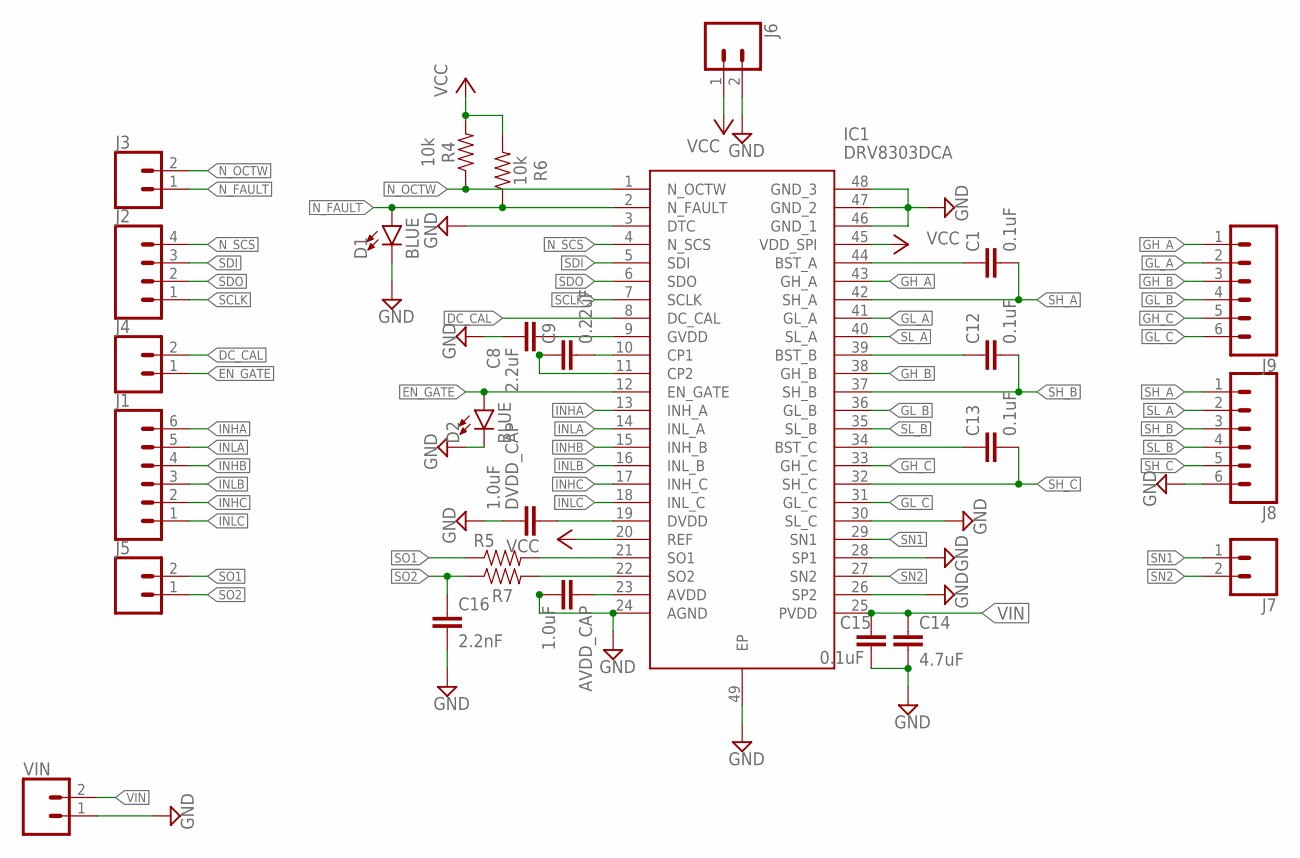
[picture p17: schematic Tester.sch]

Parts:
AVDD_CAP: 1.0uF; 0603
C1, C12, C13, C15: 0.1uF; 0603
C8: 2.2uF; 0603
C9: 0.22uF; 0603
C14: 4.7uF; 0603
C16: 2.2nF; 0603
D1, D2: BLUE; LED-0603
DVDD_CAP: 1.0uF; 0603
IC1: DRV8303DCA; SOP50P810X120-49N
J1, J8, J9: CONN_06SILK_FEMALE_PTH; 1X06
J2: CONN_04PTH; 1X04
J3, J4, J5, J6, J7: CONN_02; 1X02
R4, R6: 10k; 0603
R5, R7: 0; 0603
VIN: CONN_02LOCK_LONGPADS; 1X02_LOCK_LONGPADS

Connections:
DC_CAL: IC1.8 (DC_CAL), J4.2
EN_GATE: D2.A, IC1.12 (EN_GATE), J4.1
GH_A: IC1.43 (GH_A), J9.1
GH_B: IC1.38 (GH_B), J9.3
GH_C: IC1.33 (GH_C), J9.5
GL_A: IC1.41 (GL_A), J9.2
GL_B: IC1.36 (GL_B), J9.4
GL_C: IC1.31 (GL_C), J9.6
GND: AVDD_CAP.2, C8.2, C14.2, C15.2, C16.2, D1.C, D2.C, DVDD_CAP.1, IC1.3 (DTC), IC1.24 (AGND), IC1.26 (SP2), IC1.28 (SP1), IC1.30 (SL_C), IC1.46 (GND_1), IC1.47 (GND_2), IC1.48 (GND_3), IC1.49 (EP), J6.2, J8.6, VIN.1
INHA: IC1.13 (INH_A), J1.6
INHB: IC1.15 (INH_B), J1.4
INHC: IC1.17 (INH_C), J1.2
INLA: IC1.14 (INL_A), J1.5
INLB: IC1.16 (INL_B), J1.3
INLC: IC1.18 (INL_C), J1.1
unnamed: IC1.21 (SO1), R5.2
unnamed: C1.1, IC1.44 (BST_A)
unnamed: IC1.22 (SO2), R7.2
unnamed: C12.1, IC1.39 (BST_B)
unnamed: C13.1, IC1.34 (BST_C)
unnamed: C8.1, IC1.9 (GVDD)
unnamed: C9.2, IC1.10 (CP1)
unnamed: C9.1, IC1.11 (CP2)
unnamed: DVDD_CAP.2, IC1.19 (DVDD)
unnamed: AVDD_CAP.1, IC1.23 (AVDD)
N_FAULT: D1.A, IC1.2 (N_FAULT), J3.1, R6.1
N_OCTW: IC1.1 (N_OCTW), J3.2, R4.1
N_SCS: IC1.4 (N_SCS), J2.4
SCLK: IC1.7 (SCLK), J2.1
SDI: IC1.5 (SDI), J2.3
SDO: IC1.6 (SDO), J2.2
SH_A: C1.2, IC1.42 (SH_A), J8.1
SH_B: C12.2, IC1.37 (SH_B), J8.3
SH_C: C13.2, IC1.32 (SH_C), J8.5
SL_A: IC1.40 (SL_A), J8.2
SL_B: IC1.35 (SL_B), J8.4
SN1: IC1.29 (SN1), J7.1
SN2: IC1.27 (SN2), J7.2
SO1: J5.2, R5.1
SO2: C16.1, J5.1, R7.1
VCC: IC1.20 (REF), IC1.45 (VDD_SPI), J6.1, R4.2, R6.2
VIN: C14.1, C15.1, IC1.25 (PVDD), VIN.2

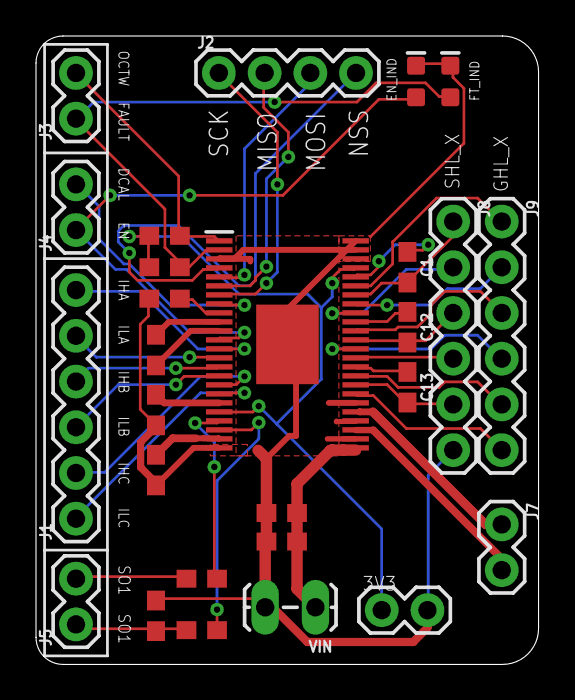
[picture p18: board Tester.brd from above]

Board: 2 copper layers, 27.9 x 34.9 mm, 27 parts (0 on the bottom side), 42 nets.

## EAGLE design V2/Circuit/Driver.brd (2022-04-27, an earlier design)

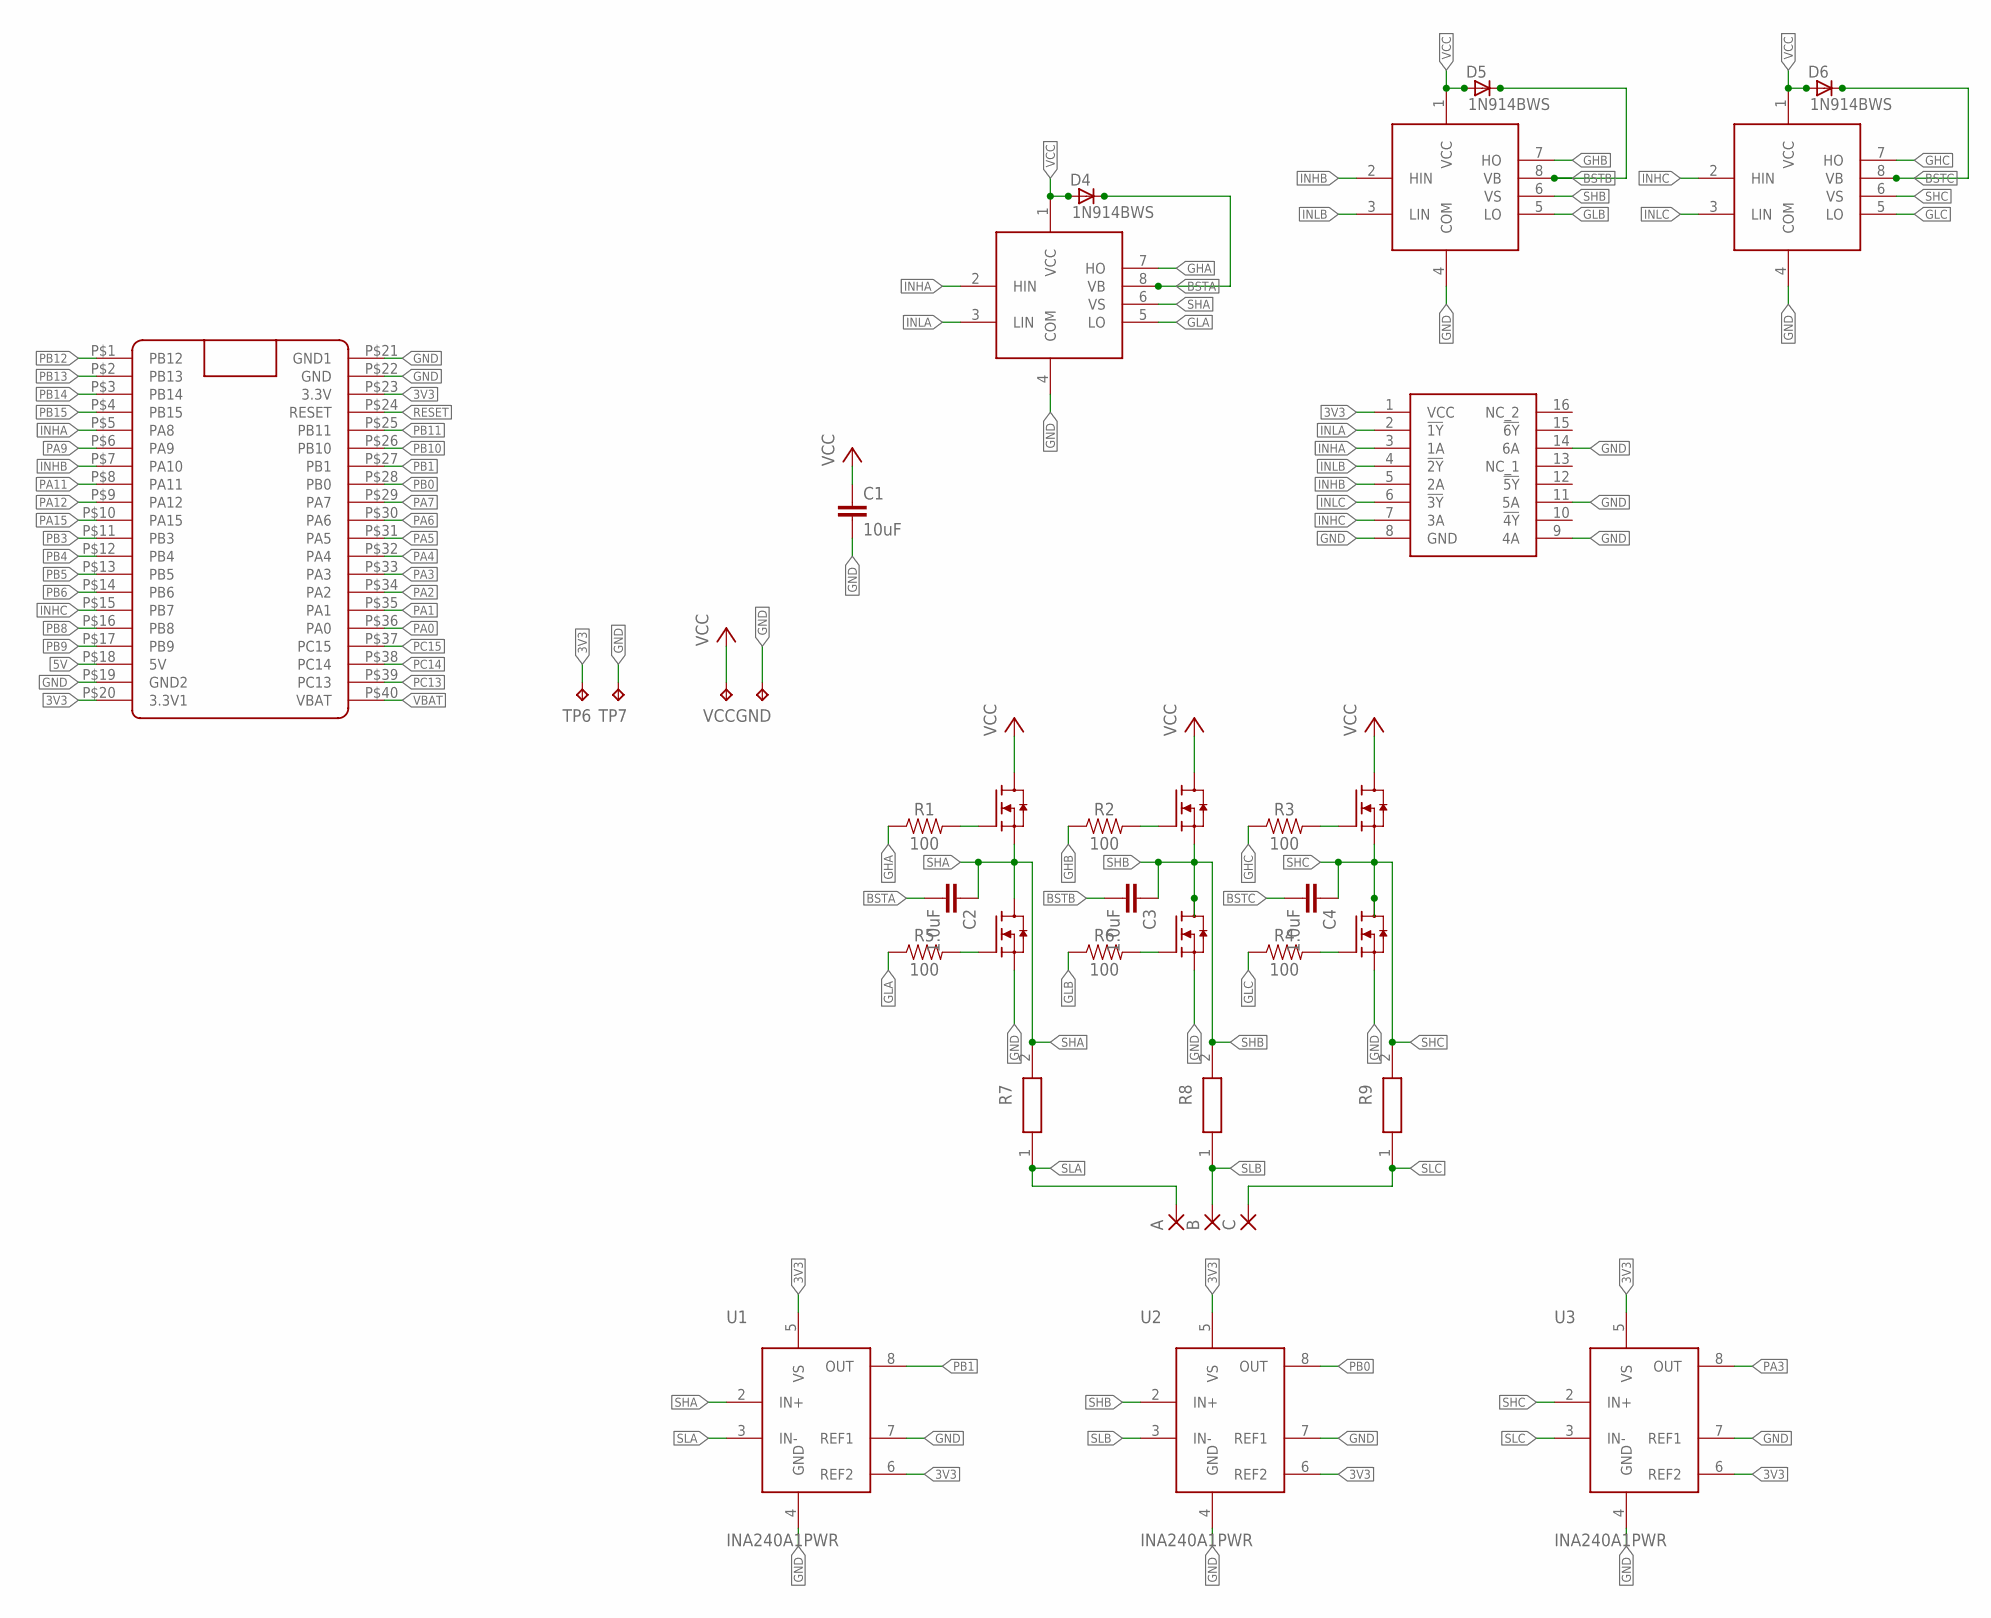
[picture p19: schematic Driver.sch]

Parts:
A: SMD5; SMD2,54-5,08
B: SMD5; SMD2,54-5,08
C: SMD5; SMD2,54-5,08
C1: 10uF; 0603
C2, C3, C4: 1.0uF; 0603
D4, D5, D6: 1N914BWS; SOD323F
GND: TPPAD1-13Y; P1-13Y
H-A: IRLR7843; TO252
H-B: IRLR7843; TO252
H-C: IRLR7843; TO252
IC2: CD74HC4049PWR; SOP65P640X120-16N
L-A: IRLR7843; TO252
L-B: IRLR7843; TO252
L-C: IRLR7843; TO252
R1, R2, R3, R4, R5, R6: 100; 0603
R7, R8, R9: CR2512-FX-51R1ELF; RESC6331X75N
TP6, TP7: TPPAD1-13Y; P1-13Y
U1, U2, U3: INA240A1PWR; SOP65P640X120-8N
U4, U5, U6: SOIC127P610X320-8NSOIC8; SOIC127P599X175-8N
U$1: BLUE_PILL
VCC: TPPAD1-13Y; P1-13Y

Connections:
3V3: IC2.1 (VCC), TP6.TP, U1.5 (VS), U1.6 (REF2), U2.5 (VS), U2.6 (REF2), U3.5 (VS), U3.6 (REF2), U$1.P$20 (3.3V1), U$1.P$23 (3.3V)
5V: U$1.P$18 (5V)
BSTA: C2.2, D4.C, U4.8 (VB)
BSTB: C3.2, D5.C, U5.8 (VB)
BSTC: C4.2, D6.C, U6.8 (VB)
GHA: R1.1, U4.7 (HO)
GHB: R2.1, U5.7 (HO)
GHC: R3.1, U6.7 (HO)
GLA: R5.1, U4.5 (LO)
GLB: R6.1, U5.5 (LO)
GLC: R4.1, U6.5 (LO)
GND: C1.2, GND.TP, IC2.8 (GND), IC2.9 (4A), IC2.11 (5A), IC2.14 (6A), L-A.2 (S), L-B.2 (S), L-C.2 (S), TP7.TP, U1.4 (GND), U1.7 (REF1), U2.4 (GND), U2.7 (REF1), U3.4 (GND), U3.7 (REF1), U4.4 (COM), U5.4 (COM), U6.4 (COM), U$1.P$19 (GND2), U$1.P$21 (GND1), U$1.P$22 (GND)
INHA: IC2.3 (1A), U4.2 (HIN), U$1.P$5 (PA8)
INHB: IC2.5 (2A), U5.2 (HIN), U$1.P$7 (PA10)
INHC: IC2.7 (3A), U6.2 (HIN), U$1.P$15 (PB7)
INLA: IC2.2 (!1Y), U4.3 (LIN)
INLB: IC2.4 (!2Y), U5.3 (LIN)
INLC: IC2.6 (!3Y), U6.3 (LIN)
unnamed: H-A.1 (G), R1.2
unnamed: H-B.1 (G), R2.2
unnamed: H-C.1 (G), R3.2
unnamed: L-A.1 (G), R5.2
unnamed: L-B.1 (G), R6.2
unnamed: L-C.1 (G), R4.2
PA0: U$1.P$36 (PA0)
PA1: U$1.P$35 (PA1)
PA2: U$1.P$34 (PA2)
PA3: U3.8 (OUT), U$1.P$33 (PA3)
PA4: U$1.P$32 (PA4)
PA5: U$1.P$31 (PA5)
PA6: U$1.P$30 (PA6)
PA7: U$1.P$29 (PA7)
PA9: U$1.P$6 (PA9)
PA11: U$1.P$8 (PA11)
PA12: U$1.P$9 (PA12)
PA15: U$1.P$10 (PA15)
PB0: U2.8 (OUT), U$1.P$28 (PB0)
PB1: U1.8 (OUT), U$1.P$27 (PB1)
PB3: U$1.P$11 (PB3)
PB4: U$1.P$12 (PB4)
PB5: U$1.P$13 (PB5)
PB6: U$1.P$14 (PB6)
PB8: U$1.P$16 (PB8)
PB9: U$1.P$17 (PB9)
PB10: U$1.P$26 (PB10)
PB11: U$1.P$25 (PB11)
PB12: U$1.P$1 (PB12)
PB13: U$1.P$2 (PB13)
PB14: U$1.P$3 (PB14)
PB15: U$1.P$4 (PB15)
PC13: U$1.P$39 (PC13)
PC14: U$1.P$38 (PC14)
PC15: U$1.P$37 (PC15)
RESET: U$1.P$24 (RESET)
SHA: C2.1, H-A.2 (S), L-A.3 (D), R7.2, U1.2 (IN+), U4.6 (VS)
SHB: C3.1, H-B.2 (S), L-B.3 (D), R8.2, U2.2 (IN+), U5.6 (VS)
SHC: C4.1, H-C.2 (S), L-C.3 (D), R9.2, U3.2 (IN+), U6.6 (VS)
SLA: A.1, R7.1, U1.3 (IN-)
SLB: B.1, R8.1, U2.3 (IN-)
SLC: C.1, R9.1, U3.3 (IN-)
VBAT: U$1.P$40 (VBAT)
VCC: C1.1, D4.A, D5.A, D6.A, H-A.3 (D), H-B.3 (D), H-C.3 (D), U4.1 (VCC), U5.1 (VCC), U6.1 (VCC), VCC.TP

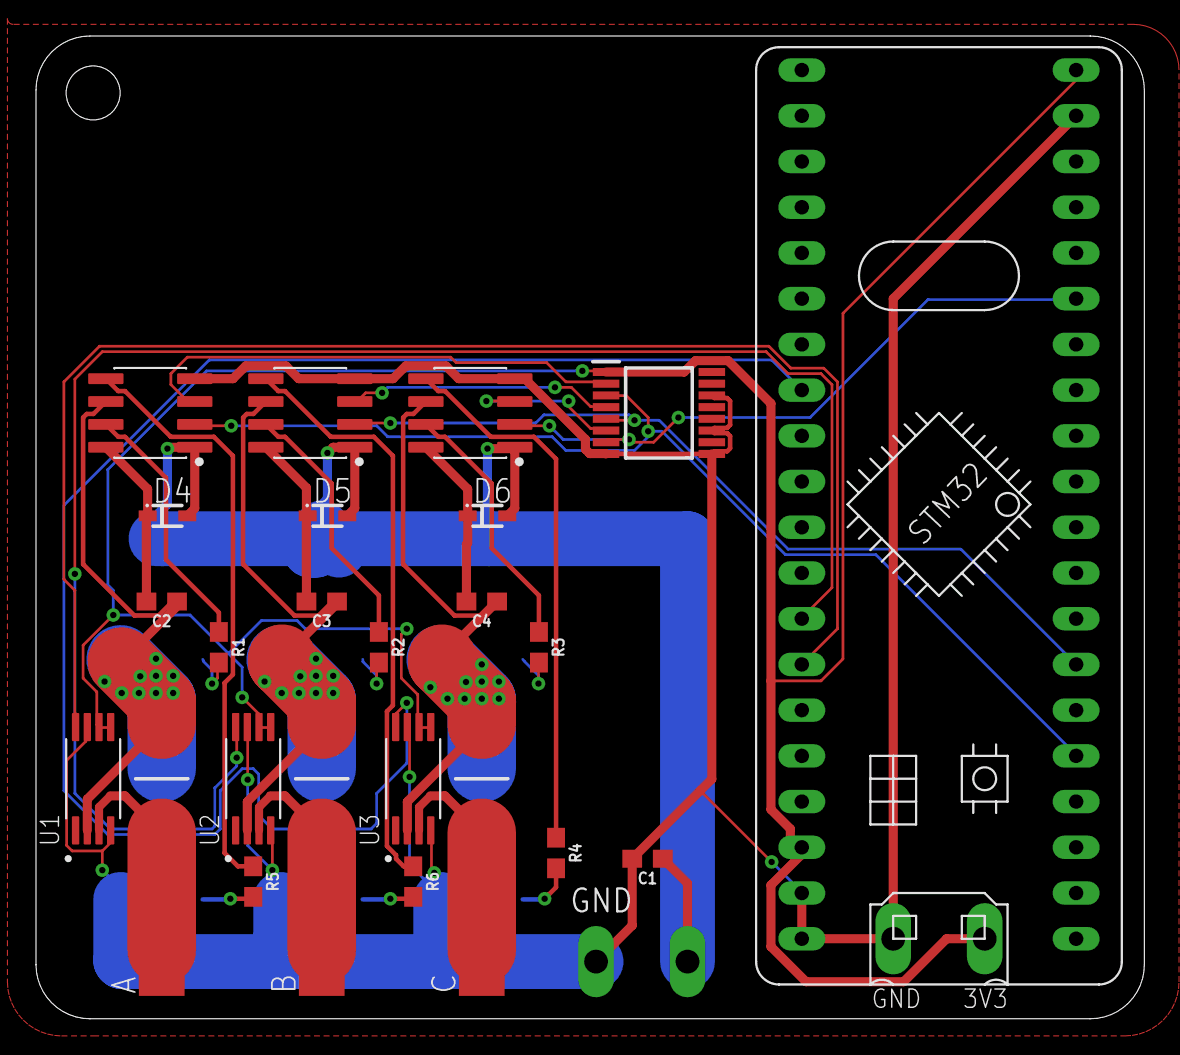
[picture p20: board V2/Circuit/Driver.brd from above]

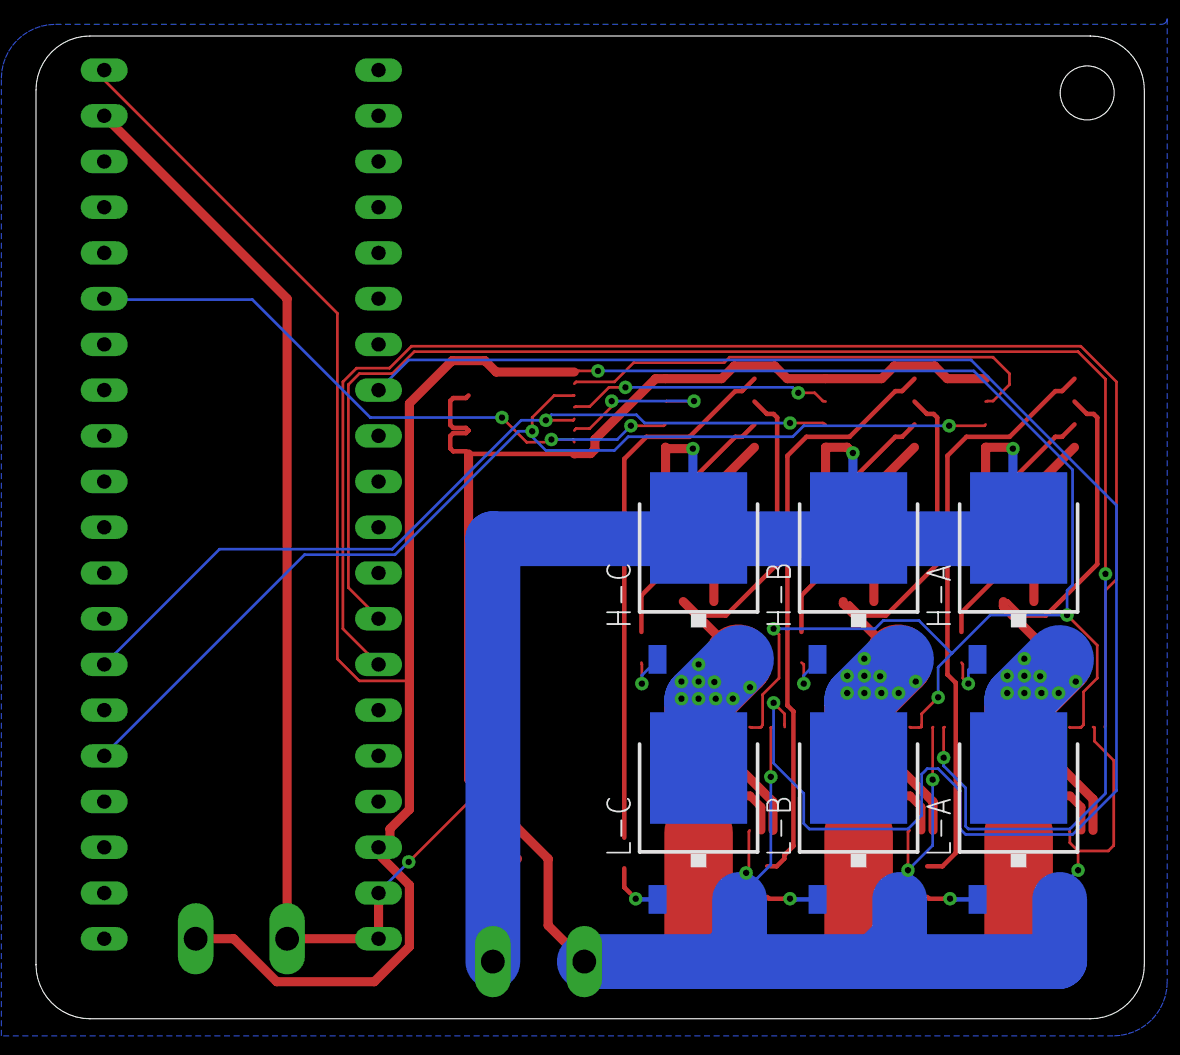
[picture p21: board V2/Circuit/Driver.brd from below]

Board: 2 copper layers, 61.6 x 54.6 mm, 37 parts (6 on the bottom side), 33 nets.

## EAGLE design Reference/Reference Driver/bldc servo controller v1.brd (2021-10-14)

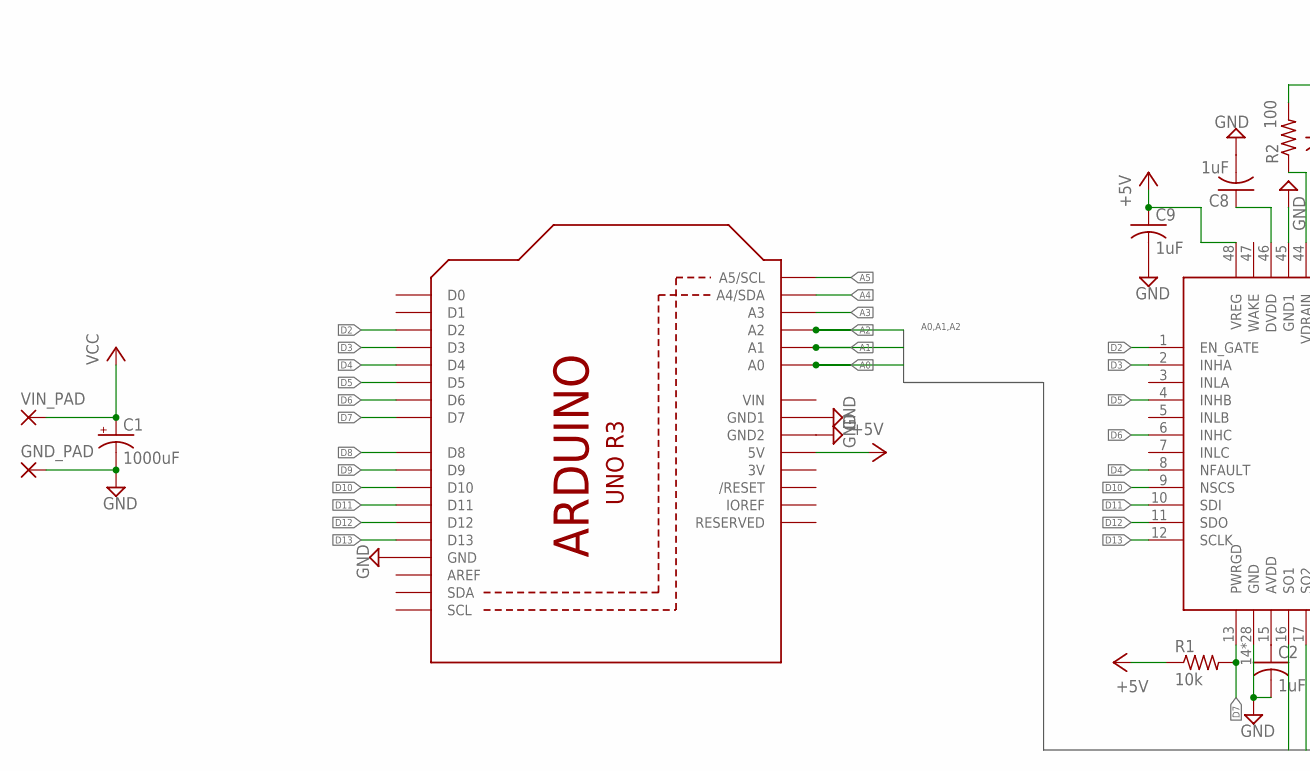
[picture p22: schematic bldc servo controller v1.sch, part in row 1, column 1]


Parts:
A: WIREPAD1,6/0,8; 1,6/0,8
B: WIREPAD1,6/0,8; 1,6/0,8
C: WIREPAD1,6/0,8; 1,6/0,8
C1: 1000uF; E3,5-10
C2, C3, C8, C9, C11, C13, C15: 1uF; C0805
C4: 2.2uF; C0805
C5: 4.7uF; C0805
C6, C7: 47nF; C0805
C10, C12, C14: 1nF; C0805
GND_PAD: WIREPAD1,6/0,8; 1,6/0,8
R1: 10k; M0805
R2: 100; M0805
R3, R4, R5: 0.5m ohm; R2512
U1: ARDUINOR3-BPLACE
U$1: DRV8305; PFB_S-PQFP-G48
U$2, U$3, U$4, U$5, U$6, U$7: IRLR7843; TO252
VIN_PAD: WIREPAD1,6/0,8; 1,6/0,8

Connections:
3V: U1.3V
+5V: C9.1, R1.1, U1.5V, U$1.48 (VREG)
A0: U1.A0, U$1.16 (SO1)
A1: U1.A1, U$1.17 (SO2)
A2: U1.A2, U$1.18 (SO3)
A3: U1.A3
A4: U1.A4 (A4/SDA)
A5: U1.A5 (A5/SCL)
D2: U1.D2, U$1.1 (EN_GATE)
D3: U1.D3, U$1.2 (INHA)
D4: U1.D4, U$1.8 (NFAULT)
D5: U1.D5, U$1.4 (INHB)
D6: U1.D6, U$1.6 (INHC)
D7: R1.2, U1.D7, U$1.13 (PWRGD)
D8: U1.D8
D9: U1.D9
D10: U1.D10, U$1.9 (NSCS)
D11: U1.D11, U$1.10 (SDI)
D12: U1.D12, U$1.11 (SDO)
D13: U1.D13, U$1.12 (SCLK)
GH_A: U$1.36 (GH_A), U$2.1 (G)
GH_B: U$1.29 (GH_B), U$4.1 (G)
GH_C: U$1.28 (GH_C), U$6.1 (G)
GL_A: U$1.33 (GL_A), U$3.1 (G)
GL_B: U$1.32 (GL-B), U$5.1 (G)
GL_C: U$1.25 (GL_C), U$7.1 (G)
GND: C1.-, C2.2, C3.2, C5.2, C8.2, C9.2, C10.2, C11.2, C12.2, C13.2, C14.2, C15.2, GND_PAD.1, R3.1, R4.1, R5.1, U1.GND, U1.GND1, U1.GND2, U$1.14 (GND), U$1.20 (SP3), U$1.22 (SP2), U$1.24 (SP1), U$1.45 (GND1), U$1.P$1 (GND), U$1.P$2 (GND), U$1.P$3 (GND), U$1.P$4 (GND), U$1.P$5 (GND), U$1.P$6 (GND), U$1.P$7 (GND), U$1.P$8 (GND), U$1.P$9 (GND), U$1.P$10 (GND), U$1.P$11 (GND), U$1.P$12 (GND), U$1.P$13 (GND), U$1.P$14 (GND), U$1.P$15 (GND), U$1.P$16 (GND), U$1.P$17 (GND), U$1.P$18 (GND), U$1.P$19 (GND), U$1.P$20 (GND), U$1.P$21 (GND), U$1.P$22 (GND), U$1.P$23 (GND), U$1.P$24 (GND), U$1.P$25 (GND), U$1.P$26 (GND), U$1.P$27 (GND)
unnamed: C2.1, U$1.15 (AVDD)
unnamed: C3.1, U$1.37 (VCP_LSD)
unnamed: C4.2, U$1.38 (VCPH)
unnamed: C6.2, U$1.40 (CP2L)
unnamed: C6.1, U$1.39 (CP2H)
unnamed: C7.2, U$1.43 (CP1H)
unnamed: C7.1, U$1.42 (CP1L)
unnamed: R2.1, U$1.44 (VDRAIN)
unnamed: C8.1, U$1.46 (DVDD)
SH_A: A.1, U$1.35 (SH_A), U$2.2 (S), U$3.3 (D)
SH_B: B.1, U$1.30 (SH_B), U$4.2 (S), U$5.3 (D)
SH_C: C.1, U$1.27 (SH_C), U$6.2 (S), U$7.3 (D)
SL_A: C10.1, R3.2, U$1.23 (SN1), U$1.34 (SL_A), U$3.2 (S)
SL_B: C12.1, R4.2, U$1.21 (SN2), U$1.31 (SL_B), U$5.2 (S)
SL_C: C14.1, R5.2, U$1.19 (SN3), U$1.26 (SL_C), U$7.2 (S)
VCC: C1.+, C4.1, C5.1, C11.1, C13.1, C15.1, R2.2, U$1.41 (PVDD), U$2.3 (D), U$4.3 (D), U$6.3 (D), VIN_PAD.1
VIN: U1.VIN



Board: 2 copper layers, 53.3 x 54.3 mm, 33 parts (8 on the bottom side), 37 nets.

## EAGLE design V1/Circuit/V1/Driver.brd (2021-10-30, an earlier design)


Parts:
5V: TP2P2-38-17; P2-38-17
A: PTR1PAD1-20Y; P1-20Y
B: PTR1PAD1-20Y; P1-20Y
C: PTR1PAD1-20Y; P1-20Y
C1, C10, C15, C16: 1uF; C0603
C2, C3, C4: 1nF; 0603
C5, C6, C7: 1.0uF; 0603
C11: 2.2uF; C0603
C12: 4.7uF; C0603
C13, C14: 47nF; C0603
JP1, JP2: PINHD-1X12; 1X12
R1, R2, R5: R-EU_R2512; R2512
R3: 10k; R0603
R4: 100; R0603
R6: 10k; 0603
TP1, TP2: PTR1PAD1-20Y; P1-20Y
U$1: BLUE_PILLADVANCED; BLUE_PILL_ADV
U$2, U$4, U$5, U$6, U$7, U$8: IRLR7843; TO252
U$3: DRV8305; PFB_S-PQFP-G48

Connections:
CP1H: C14.2, U$3.43 (CP1H)
CP1L: C14.1, U$3.42 (CP1L)
CP2H: C13.1, U$3.39 (CP2H)
CP2L: C13.2, U$3.40 (CP2L)
DVDD: C15.1, U$3.46 (DVDD)
GH_A: JP1.1, U$2.1 (G), U$3.36 (GH_A)
GH_B: JP1.8, U$3.29 (GH_B), U$5.1 (G)
GH_C: JP1.9, U$3.28 (GH_C), U$7.1 (G)
GL_A: JP1.4, U$3.33 (GL_A), U$4.1 (G)
GL_B: JP1.5, U$3.32 (GL-B), U$6.1 (G)
GL_C: JP1.12, U$3.25 (GL_C), U$8.1 (G)
GND: 5V.TP-1, C1.2, C2.1, C3.1, C4.1, C5.2, C6.2, C7.2, C10.2, C12.2, C15.2, C16.2, R1.1, R2.1, R5.1, TP2.TP, U$1.P$19 (GND2), U$1.P$21 (GND1), U$1.P$22 (GND), U$3.14 (GND), U$3.20 (SP3), U$3.22 (SP2), U$3.24 (SP1), U$3.45 (GND1), U$3.P$1 (GND), U$3.P$2 (GND), U$3.P$3 (GND), U$3.P$4 (GND), U$3.P$5 (GND), U$3.P$6 (GND), U$3.P$7 (GND), U$3.P$8 (GND), U$3.P$9 (GND), U$3.P$10 (GND), U$3.P$11 (GND), U$3.P$12 (GND), U$3.P$13 (GND), U$3.P$14 (GND), U$3.P$15 (GND), U$3.P$16 (GND), U$3.P$17 (GND), U$3.P$18 (GND), U$3.P$19 (GND), U$3.P$20 (GND), U$3.P$21 (GND), U$3.P$22 (GND), U$3.P$23 (GND), U$3.P$24 (GND), U$3.P$25 (GND), U$3.P$26 (GND), U$3.P$27 (GND)
unnamed: C1.1, U$3.15 (AVDD)
PA0: U$1.P$36 (PA0)
PA1: U$1.P$35 (PA1)
PA2: U$1.P$34 (PA2)
PA3: U$1.P$33 (PA3), U$3.18 (SO3)
PA4: JP2.4, U$1.P$32 (PA4), U$3.9 (NSCS)
PA5: JP2.1, U$1.P$31 (PA5), U$3.12 (SCLK)
PA6: JP2.2, U$1.P$30 (PA6), U$3.11 (SDO)
PA7: JP2.3, U$1.P$29 (PA7), U$3.10 (SDI)
PA8: JP2.11, U$1.P$5 (PA8), U$3.2 (INHA)
PA9: JP2.10, U$1.P$6 (PA9), U$3.3 (INLA)
PA10: JP2.9, U$1.P$7 (PA10), U$3.4 (INHB)
PA11: U$1.P$8 (PA11)
PA12: U$1.P$9 (PA12)
PA15: U$1.P$10 (PA15)
PB0: U$1.P$28 (PB0), U$3.17 (SO2)
PB1: U$1.P$27 (PB1), U$3.16 (SO1)
PB3: U$1.P$11 (PB3)
PB4: U$1.P$12 (PB4)
PB5: U$1.P$13 (PB5)
PB6: JP2.8, U$1.P$14 (PB6), U$3.5 (INLB)
PB7: JP2.7, U$1.P$15 (PB7), U$3.6 (INHC)
PB8: JP2.6, U$1.P$16 (PB8), U$3.7 (INLC)
PB9: U$1.P$17 (PB9)
PB10: U$1.P$26 (PB10)
PB11: U$1.P$25 (PB11)
PB12: JP2.12, U$1.P$1 (PB12), U$3.1 (EN_GATE)
PB13: JP2.5, R6.2, U$1.P$2 (PB13), U$3.8 (NFAULT)
PB14: U$1.P$3 (PB14)
PB15: U$1.P$4 (PB15)
PC13: U$1.P$39 (PC13)
PC14: U$1.P$38 (PC14)
PC15: U$1.P$37 (PC15)
PWRGD: R3.2, U$3.13 (PWRGD)
SH_A: A.TP, JP1.2, U$2.2 (S), U$3.35 (SH_A), U$4.3 (D)
SH_B: B.TP, JP1.7, U$3.30 (SH_B), U$5.2 (S), U$6.3 (D)
SH_C: C.TP, JP1.10, U$3.27 (SH_C), U$7.2 (S), U$8.3 (D)
SN1: C2.2, JP1.3, R1.2, U$3.23 (SN1), U$3.34 (SL_A), U$4.2 (S)
SN2: C3.2, JP1.6, R2.2, U$3.21 (SN2), U$3.31 (SL_B), U$6.2 (S)
SN3: C4.2, JP1.11, R5.2, U$3.19 (SN3), U$3.26 (SL_C), U$8.2 (S)
VCC: 5V.TP-2, C16.1, R3.1, R6.1, U$1.P$18 (5V), U$3.48 (VREG)
VCPH: C11.2, U$3.38 (VCPH)
VCP_LSD: C10.1, U$3.37 (VCP_LSD)
VDRAIN: R4.1, U$3.44 (VDRAIN)
VIN: C5.1, C6.1, C7.1, C11.1, C12.1, R4.2, TP1.TP, U$2.3 (D), U$3.41 (PVDD), U$5.3 (D), U$7.3 (D)



Board: 2 copper layers, 84.5 x 61.9 mm, 36 parts (9 on the bottom side), 40 nets.

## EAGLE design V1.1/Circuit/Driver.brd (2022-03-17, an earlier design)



Board: 2 copper layers, 61.6 x 54.6 mm, 32 parts (6 on the bottom side), 33 nets.

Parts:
A: SMD2,54-5,08
B: SMD2,54-5,08
C: SMD2,54-5,08
C1: 10uF; 0603
C2, C3, C4: 1.0uF; 0603
GND: TPPAD1-13Y; P1-13Y
IC1: DRV8300DIPWR; SOP65P640X120-20N
IC2: CD74HC4049PWR; SOP65P640X120-16N
R1, R2, R3, R4, R5, R6: 100; 0603
R7, R8, R9: CR2512-FX-51R1ELF; RESC6331X75N
TP6, TP7: TPPAD1-13Y; P1-13Y
U1, U2, U3: INA240A1PWR; SOP65P640X120-8N
U$1: BLUE_PILL
U$2, U$3, U$4, U$5, U$6, U$7: IRLR7843; TO252
VCC: TPPAD1-13Y; P1-13Y

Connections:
3V3: IC2.1, TP6.TP, U1.5, U1.6, U2.5, U2.6, U3.5, U3.6, U$1.P$20, U$1.P$23
BSTA: C2.2, IC1.20
BSTB: C3.2, IC1.17
BSTC: C4.2, IC1.14
GHA: IC1.19, R1.1
GHB: IC1.16, R2.1
GHC: IC1.13, R3.1
GLA: IC1.11, R5.1
GLB: IC1.10, R6.1
GLC: IC1.9, R4.1
GND: C1.2, GND.TP, IC1.8, IC2.8, IC2.9, IC2.11, IC2.14, TP7.TP, U1.4, U1.7, U2.4, U2.7, U3.4, U3.7, U$1.P$19, U$1.P$21, U$1.P$22, U$3.2, U$5.2, U$7.2
INHA: IC1.1, IC2.3, U$1.P$5
INHB: IC1.2, IC2.5, U$1.P$7
INHC: IC1.3, IC2.7, U$1.P$15
INLA: IC1.4, IC2.2
INLB: IC1.5, IC2.4
INLC: IC1.6, IC2.6
unnamed: R1.2, U$2.1
unnamed: R2.2, U$4.1
unnamed: R3.2, U$6.1
unnamed: R5.2, U$3.1
unnamed: R6.2, U$5.1
unnamed: R4.2, U$7.1
PA3: U3.8, U$1.P$33
PB0: U2.8, U$1.P$28
PB1: U1.8, U$1.P$27
SHA: C2.1, IC1.18, R7.2, U1.2, U$2.2, U$3.3
SHB: C3.1, IC1.15, R8.2, U2.2, U$4.2, U$5.3
SHC: C4.1, IC1.12, R9.2, U3.2, U$6.2, U$7.3
SLA: A.1, R7.1, U1.3
SLB: B.1, R8.1, U2.3
SLC: C.1, R9.1, U3.3
VCC: C1.1, IC1.7, U$2.3, U$4.3, U$6.3, VCC.TP

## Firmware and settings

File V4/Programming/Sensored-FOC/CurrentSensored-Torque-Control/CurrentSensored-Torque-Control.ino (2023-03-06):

#include <SimpleFOC.h>
#include <SPI.h>

#include <MovingAverage.h>

#include <string>

#define INHA PA8
#define INLA PB6
#define SO1 PA1

#define INHB PA9
#define INLB PB7
#define SO2 PA0

#define INHC PA10
#define INLC PB8

#define NFAULT PB13
#define NOCTW PB14

#define EN_GATE PB12
#define DC_CAL PB4

#define LED PC13

#define chipSelectPin PA4
#define A PA11
#define B PA12
#define Index PA15

#define LED PC13

word data;

BLDCMotor motor = BLDCMotor(7);
BLDCDriver3PWM driver = BLDCDriver3PWM(INHA, INHB, INHC, EN_GATE);

LowsideCurrentSense current_sense = LowsideCurrentSense(0.00658395332, -20, SO1, SO2);

Encoder encoder = Encoder(A, B, 1000, Index);

void doA() { encoder.handleA(); }
void doB() { encoder.handleB(); }
void doIndex() { encoder.handleIndex(); }
HardwareSerial Serial3(PA3, PA2);

MovingAverage CurrentAmpliferA(1);
MovingAverage CurrentAmpliferB(1);

void setup()
{
    //================MCU and DRV8303 setup Below================
    Serial3.begin(115200);
    pinMode(EN_GATE, OUTPUT);
    pinMode(NFAULT, INPUT);
    pinMode(NOCTW, INPUT);
    pinMode(DC_CAL, OUTPUT);

    digitalWrite(EN_GATE, HIGH);

    delay(1);
    SPI_SETUP();
    delay(10);
    changeSPIGAIN2_20();
    changeSPI();
    //================MCU and DRV8303 setup Above================

    //================SimpleFOC setup Below================
    // encoder.quadrature = Quadrature::ON;
    encoder.init();
    encoder.enableInterrupts(doA, doB, doIndex);

    motor.linkSensor(&encoder);

    Serial3.println("Encoder ready");

    driver.voltage_power_supply = 12;
    driver.voltage_limit = 3;

    driver.init();

    motor.linkDriver(&driver);
    //-----------------Current Sensor Setup Below-----------------
    pinMode(SO1, INPUT);
    pinMode(SO2, INPUT);
    digitalWrite(DC_CAL, LOW);

    current_sense.skip_align = true;

    current_sense.linkDriver(&driver);

    current_sense.init();

    motor.linkCurrentSense(&current_sense);
    //-----------------Current Sensor Setup Above-----------------

    // limiting motor current (provided resistance)
    motor.voltage_sensor_align = 0.6;

    motor.foc_modulation = FOCModulationType::SinePWM;
    motor.torque_controller = TorqueControlType::foc_current;
    motor.controller = MotionControlType::torque;

    //======================P axis and D axis PID below======================
    motor.PID_current_q.P = 1;
    motor.PID_current_q.I = 0.2;

    motor.PID_current_d.P = 0;
    motor.PID_current_d.I = 0;

    motor.LPF_current_q.Tf = 0.02;
    motor.LPF_current_d.Tf = 0.03;

    motor.useMonitoring(Serial3);
    motor.monitor_variables = _MON_CURR_Q | _MON_CURR_D;
    motor.sensor_direction = Direction::CW;
    motor.monitor_downsample = 1; // default 10

    motor.init();
    motor.initFOC();
    Serial3.println("Motor ready");
    Serial3.println(motor.sensor_direction);
    delay(4000);
    //================SimpleFOC setup Above================
}

void loop()
{
    motor.loopFOC();
    motor.move(0.5);
    motor.monitor();
    // Serial3.print("\t");
    // GetAndPrintCurrentValue();
    // Serial3.println(encoder.getMechanicalAngle());

    // Serial3.println(motor.electricalAngle());
}

void GetAndPrintCurrentValue()
{
    PhaseCurrent_s currents = current_sense.getPhaseCurrents();

    Serial3.print(currents.a, 6); // milli Amps
    Serial3.print("\t");
    Serial3.print(currents.b, 6); // milli Amps
    Serial3.print("\t");
    Serial3.print(-currents.a - currents.b, 6);
    Serial3.print("\t");
}

void GetAndPrint_FOC_CurrentValue(float angle_el)
{
    DQCurrent_s currents = current_sense.getFOCCurrents(angle_el);
    // Serial3.print("ElectricalAngle:");
    // Serial3.print(angle_el, 6); // milli Amps
    // Serial3.pr   int("\t");
    // Serial3.print();          // milli Amps
    Serial3.print(currents.q, 6); // milli Amps
    Serial3.print("\t");
    // Serial3.print("Q:");            // milli Amps
    Serial3.println(currents.d, 6); // milli Amps
    // Serial3.print("\t");
}

// void GetAndPrint_AnalogReadCurrentValue()
// {
//     Serial3.print("A:");
//     Serial3.print(GetShuntResistorVoltage(CurrentAmpliferA.addSample((analogRead(SO1) / 1023. * 3.3) + offsetA)) / 0.05E-3, 6);
//     Serial3.print(",B:");
//     Serial3.println(GetShuntResistorVoltage(CurrentAmpliferB.addSample((analogRead(SO2) / 1023. * 3.3) + offsetB)) / 0.05E-3, 6);
// }

double GetShuntResistorVoltage(double RawVolt)
{
    const double G = 80.;
    const double VREF = 3.3;
    return ((VREF / 2.) - RawVolt) / G; // general solve
}

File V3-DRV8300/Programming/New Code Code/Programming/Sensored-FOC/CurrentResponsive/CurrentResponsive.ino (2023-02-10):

#include <SimpleFOC.h>
#include <MovingAverage.h>

#include <SPI.h>

#define INHA PA8
#define INLA PB6
#define SO1 PA1

#define INHB PA9
#define INLB PB7
#define SO2 PA0

#define INHC PA10
#define INLC PB8

#define NFAULT PB13
#define NOCTW PB14

#define EN_GATE PB12
#define DC_CAL PB4

#define LED PC13

#define chipSelectPin PA4
word data;

BLDCMotor motor = BLDCMotor(6);
BLDCDriver3PWM driver = BLDCDriver3PWM(INHA, INHB, INHC, EN_GATE);

HardwareSerial Serial3(PA3, PA2);

MovingAverage CurrentAmpliferA(1);
MovingAverage CurrentAmpliferB(1);

// target variable
float target_velocity = -70;

void changeSPI()
{
    digitalWrite(chipSelectPin, LOW);          // manually take CSN low for SPI_1 transmission
    data = SPI.transfer16(0b0001000000001000); // 0 0010 00000001000
    digitalWrite(chipSelectPin, HIGH);         // manually take CSN high between spi transmissions
}

void changeSPIGAIN2_80()
{
    digitalWrite(chipSelectPin, LOW);          // manually take CSN low for SPI_1 transmission
    data = SPI.transfer16(0b0001100000001100); // 0 0011 00000001000
    digitalWrite(chipSelectPin, HIGH);         // manually take CSN high between spi transmissions
}

void changeSPIGAIN2_40()
{
    digitalWrite(chipSelectPin, LOW);          // manually take CSN low for SPI_1 transmission
    data = SPI.transfer16(0b0001100000001000); // 0 0011 00000001000
    digitalWrite(chipSelectPin, HIGH);         // manually take CSN high between spi transmissions
}

void ReadSPI()
{
    digitalWrite(chipSelectPin, LOW);          // manually take CSN low for SPI_1 transmission
    data = SPI.transfer16(0b1001000000000000); // 1 0010 00000000000
    digitalWrite(chipSelectPin, HIGH);         // manually take CSN high between spi transmissions
}

void ReadStatus()
{
    digitalWrite(chipSelectPin, LOW);          // manually take CSN low for SPI_1 transmission
    data = SPI.transfer16(0b1000000000000000); // 1 0010 00000001000
    digitalWrite(chipSelectPin, HIGH);         // manually take CSN high between spi transmissions
}

void SPI_SETUP()
{
    SPI.begin();
    SPI.setBitOrder(MSBFIRST);
    SPI.setDataMode(SPI_MODE1);
    SPI.setClockDivider(SPI_CLOCK_DIV16);
    pinMode(chipSelectPin, OUTPUT);
}

double offsetA = 0.050946;
double offsetB = 0.050946;
void setup()
{
    Serial3.begin(115200);

    pinMode(INHA, OUTPUT);
    pinMode(INLA, OUTPUT);
    pinMode(SO1, INPUT);

    pinMode(INHB, OUTPUT);
    pinMode(INLB, OUTPUT);
    pinMode(SO2, INPUT);

    pinMode(INHC, OUTPUT);
    pinMode(INLC, OUTPUT);

    pinMode(EN_GATE, OUTPUT);
    pinMode(DC_CAL, OUTPUT);

    pinMode(LED, OUTPUT);
    pinMode(NFAULT, INPUT);
    pinMode(NOCTW, INPUT);

    digitalWrite(DC_CAL, LOW);

    driver.voltage_power_supply = 12;
    driver.voltage_limit = 12;
    driver.init();

    motor.linkDriver(&driver);

    motor.voltage_limit = 12; // [V]

    motor.foc_modulation = FOCModulationType::SpaceVectorPWM;
    motor.controller = MotionControlType::velocity_openloop;

    // init motor hardware
    motor.init();

    SPI_SETUP();
    changeSPIGAIN2_40();
    delay(1000);
    changeSPI();
}

int Timer = millis();

float i = 1;

void loop()
{
    if (millis() - Timer >= 300)
    {
        if (i == 1)
        {
            i = 0;
        }
        else
        {
            i = 1;
        }
        Timer = millis();
    }

    driver.setPwm(i, 0, 0);
    // Serial3.print("A:");
    // Serial3.print(GetShuntResistorVoltage(CurrentAmpliferA.addSample((analogRead(SO1) / 1023. * 3.3))) / 0.05e-3, 6);
    // Serial3.print(",B:");
    // Serial3.println(GetShuntResistorVoltage(CurrentAmpliferB.addSample((analogRead(SO2) / 1023. * 3.3))) / 0.05e-3, 6);
    Serial3.print("A:");
    Serial3.print(GetShuntResistorVoltage(((analogRead(SO1) / 1023. * 3.3) + offsetA)) / 0.5E-3, 6);
    Serial3.print(",B:");
    Serial3.println(GetShuntResistorVoltage(((analogRead(SO2) / 1023. * 3.3) + offsetB)) / 0.5E-3, 6);
}

double GetShuntResistorVoltage(double RawVolt)
{
    const double G = 40.;
    const double VREF = 3.3;
    return ((VREF / 2.) - RawVolt) / G; // general solve
}

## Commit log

2021-10-14 Create Folder and Notes, and add some prepare works for Circuit (Add a 'Blue Pill')
    [Driver.brd, Driver.sch, Reference.brd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]
2021-10-15 Add the mosfets and their driver to the BLDC Driver sch
    [Driver.brd, Driver.sch, Reference.brd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]
2021-10-17 Finish drawing the PCB for 1 stage(not add external layer yet, not autoroutering yet)
    [Driver.brd, Driver.sch]
2021-10-19 before adding pinhead
    [Driver.sch]
2021-10-21 enlarged the width of the vin and added a T-stop wire for large current signal (mosfet GND and VCC)
    [Driver.brd, Driver.sch]
2021-10-21 add a 5V pad input, delete the connection of Vin and Vbat, and add Description in Tname
    [Driver.brd]
2021-10-21 fixed some bugs(Erc and Drc Errors)
    [Driver.brd, Driver.sch]
2021-10-21 Fixed the PVDD and VDrain pin's 'Vin' problem, Fixed some bugs
    [Driver.brd, Driver.sch]
2021-10-21 Add polygon Ratsnest
    [Driver.brd]
2021-10-21 Adding CAM Output Files for V1. Delete some Eagle build-in History files
    [copper_bottom.gbr, copper_top.gbr, drill_1_16.xln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]
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2021-10-30 Folder rearrange
    [Driver.brd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]
2021-11-04 tested DRV8305's pin AH BL enable. But not working because of the overcurrent protecting
    [Enable_AH_BL_test.ino]
2021-11-07 Trying to change the config of DRV8305, but seems that the overcurrent problem doesn't go well
    [Enable_AH_BL_test.ino, OverCurrent_Test.ino]
2021-11-07 Added a PDF about my V1 Testing circuit.
    [gerber_job.gbrjob]
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2021-11-08 Finally found the solution (The problem isn't about overcurrent. The PVDD_UVLO2 fault is the one.) (Tried to disable the PVDD_UVLO2 setting, but because of the current limitation of Power Supply, The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
    [OverCurrent_Test.ino]
2021-11-09 After Changing the PVDD_UVLO2 config, I manually input the sequence of the BLDC motor rotations, success fully rotate the BLDC, but there are some vibration.
    [Enable_AH_BL_test.ino, OverCurrent_Test.ino]
2021-11-13 Successfully rotate the BLDC
    Successfully rotate the BLDC using FOC (*only work in 3 PWM mode*). Fix the library bug by changing the C++ file of the Simple FOC library in the Library_Specify folder.
    [open_loop_velocity_example.ino]
2021-12-30 Code-Update
    Update
    [Motor-Mount.3mf]
2021-12-30 Preparation of the V2 Driver Circuit board
    [Driver.brd, Driver.sch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]
2021-12-31 Designed and auto routed BLDC driver V2 circuit
    [Driver.brd, Driver.sch]
2021-12-31 Deleted all the autorouting signal
    [Driver.brd]
2021-12-31 Manually routed the Shunt resistor detection signal to the Gate driver
    [Driver.brd]
2021-12-31 Fix some routering bug
    [Driver.brd]
2021-12-31 Mirror the PCB arrangement
    [Driver.brd]
2022-01-08 Generated the CAM file of the V2 board
    [Driver.brd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]
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2022-01-10 Tidy up the code and prepared for V3 circuit board
    [Driver.brd, Driver.sch]
2022-01-13 Change the orginal motor gate driver(DRV8305) to DRV8303 in schematic
    [Driver.brd, Driver.sch]
2022-01-13 Routing the basic circuit and route. A backup before autorouting
    [Driver.brd, Driver.sch]
2022-01-14 Fixed some bugs and edited the note.md
    [Driver.brd, Driver.sch]
2022-01-14 Fixed some bugs
    [Driver.brd, Driver.sch]
2022-01-14 autorouted the circuit
    [Driver.brd, Driver.sch]
2022-01-29 Preparation for DRV8303
    [Driver.brd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]
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2022-03-05 New Version-Preparation
    [Driver.brd, Driver.sch, Motor-Mount.3mf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]
2022-03-05 Circuit preparation (Added stm32 and DRV8300)
    [Driver.brd, Driver.sch, Reference.brd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]
2022-03-11 Circuit: Added DRV8300, and the Gate Circuit. Haven't added the Not gate
    [Driver.brd, Driver.sch]
2022-03-11 Added the FOC library
    [Driver.brd, Driver.sch]
2022-03-12 Added Not Gate to the circuit
    [Driver.brd, Driver.sch]
2022-03-16 Ready for autoroutering
    [Driver.brd, Driver.sch]
2022-03-16 Ready for autoroutering 2
    [Driver.brd]
2022-03-16 Ready for autoroutering 3
    [Driver.brd]
2022-03-16 Ready for autoroutering 4
    [Driver.brd]
2022-03-16 Ready for autoroutering 5
    [Driver.brd]
2022-03-17 Ready for autoroutering 6
    [Driver.brd]
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2022-04-02 Prepared for V2
    [Driver.brd, Driver.sch]
2022-04-02 Designed V2, Ready for autoroutering 1
    [Driver.brd, Driver.sch]
2022-04-02 Designed V2, Ready for autoroutering 2
    [Driver.brd]
2022-04-27 Generated the Gerber files of the circuit
    [Driver.brd, Driver.sch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]
2022-07-16 Ready for V3-DRV8303
    [Driver.brd, Driver.sch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]
2022-07-16 Prepared for V3-DRV8300 PCB routing
    [Driver.brd, Driver.sch]
2022-07-16 Prepared for V3-DRV8300 PCB routing 3
    [Driver.brd]
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2022-07-17 Removed the signal than blocks the AGND to the powerpad; Ready for autorouting
    [Driver.brd]
2022-07-17 Moving two vias, the AGND signal have a better conductivity to the power pad
    [Driver.brd]
2022-07-17 Generated the V3.1 DRV8303 Gerber files
    [Driver.brd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]
2022-08-22 Prepare for DRV8303 Tester board
    [Driver.brd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]
2022-08-23 Ready for autoroutering (Tester)
    [Tester.brd, Tester.sch]
2022-08-23 Ready for autoroutering (Tester) 2
    [Tester.brd]
2022-08-23 Ready for autoroutering (Tester) 3
    [Tester.brd]
2022-08-23 Ready for autoroutering (Tester) 4
    [Tester.brd]
2022-08-23 Ready for autoroutering (Tester) 5
    [Tester.brd]
2022-08-23 Ready for autoroutering (Tester) 6
    [Tester.brd]
2022-08-23 Ready for autoroutering (Tester) 7
    [Tester.brd]
2022-08-23 Autoroutered the tester board
    [Tester.brd]
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2022-08-23 Generated Gerber file v2 (with via masked)
    [gerber_job.gbrjob]
2022-08-23 Generated Gerber file v3 (deleted bottom polygon signal)
    [Tester.brd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]
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2022-10-08 Changed all the PWM output pin to the same timer, Added 2 selector for C.S.A.
    [Driver.brd, Driver.sch]
2022-10-08 Ready for auto routering 2
    [Driver.brd]
2022-10-08 Routed all signal, ready for gerber gen
    [Driver.brd]
2022-10-08 Fixed a little mistake/bug (PA2 -> PA0)
    [Driver.brd, Driver.sch]
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2022-12-21 Ready for V4 autoroutering
    [Driver.brd, Driver.sch]
2022-12-21 Ready for V4 autoroutering 4
    [Driver.brd]
2022-12-21 Ready for V4 autoroutering 5
    [Driver.brd]
2022-12-21 Ready for V4 autoroutering 7
    [Driver.brd]
2022-12-21 Ready for V4 autoroutering 8
    [Driver.brd]
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2022-12-22 Exported a new version V4 circuit [Changes: Added a new ratsnest]
    [Driver.brd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]
2023-01-19 Velocity Closed Loop successed (with sensorless FOC and without proper PID tuning) Motor gets stuck when Target velocity rises above 90
    [Body1.stl, Body2.stl, Invoices.xlsx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]
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2023-01-19 Failed to use Simple FOC's lowsidecurrent sense to sense current
    [Current-Sensor-Test.ino, Current_Amplifier_InputVolt2Current.ino]
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2023-02-01 Successed! Found that the problem is about the value of Gain, change Gain: 10 -> 80 because 0.05mohm is too small with 10V gain, the noise overlapped the amplified signal
    [Current-Sensor-Test.ino, CurrentResponsive.ino, TestSensorWithVelocityControl.ino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]
2023-02-10 Tuned Uq Ud pid in The folder{CurrentSensored-Torque-Control} (Not perfect but works somehow)
    [Rgate_calculation.xlsx]

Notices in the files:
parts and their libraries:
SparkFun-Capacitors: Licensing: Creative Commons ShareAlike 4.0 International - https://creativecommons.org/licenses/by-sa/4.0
